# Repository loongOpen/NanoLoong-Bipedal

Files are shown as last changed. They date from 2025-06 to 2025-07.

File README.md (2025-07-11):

# NanoLoong-Bipedal
Building a high-performance bipedal robot that combines Pixar and Disney BDX！
<table>
  <tr>
    <td> </td>
    <td> </td>
    <td> </td>
   </tr> 
</table>

In this project, we combined Pixar's lamp robot and Disney's BDX robot to build a 60cm high-performance Nano bipedal robot.</br>
The entire robot uses a brushless motor, runs a reinforcement learning algorithm and comes with an open source tutorial. The cost of the whole machine is less than 15,000 RMB!</br>
This project will update the latest information in real time in the Feishu link below[https://hcn64ij2s2xr.feishu.cn/wiki/AZJxwlvEpiWnRrkeBbGc21U9n7f]</br>
Detail intro:</br>
https://www.bilibili.com/video/BV1FRZoY1ExW/?spm_id_from=333.337.search-card.all.click

# State of sim2real
The gait of Nano version is highly consistent with the BDX effect ! 

https://private-user-images.githubusercontent.com/16828431/430457828-f0ea37f3-0f17-4512-8b72-3c25d8892571.mp4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

https://private-user-images.githubusercontent.com/16828431/430457885-5fd6a661-4399-4f3d-8686-e99e13dff1be.mp4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

# Updates
> Update 2025/4/5: You can try two policies we trained : Update Nano first release version.

# CAD
https://private-user-images.githubusercontent.com/16828431/430457786-0a5316d1-bd46-40a6-932d-3f43c3e6b83e.mp4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

See [this document](https://hcn64ij2s2xr.feishu.cn/wiki/DPWDwNWaZiGNvpkbRrGcBXCHn7d) for getting from the CAD design of Nano.

# PCB
https://private-user-images.githubusercontent.com/16828431/430457807-14ccab23-9aa0-415d-9c31-68c5db94b0f6.mp4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

See [this document](https://hcn64ij2s2xr.feishu.cn/wiki/DPWDwNWaZiGNvpkbRrGcBXCHn7d) for getting from the PCB design of Nano.

# RL stuff
We are switching to IsaccGym, see this [repo](https://hcn64ij2s2xr.feishu.cn/wiki/LJxZwgL1diHB8ykKU1acFnXknOf)

https://private-user-images.githubusercontent.com/16828431/430457843-6a1d952e-9353-46ef-b826-be9859c01c90.mp4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

https://private-user-images.githubusercontent.com/16828431/430457815-24d15ffc-5014-4805-8926-c6f4ba6477bd.mp4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

## AI xiaozhi with LLM
Robots can install Xiaozhi AI modules to implement large language model functions !

https://private-user-images.githubusercontent.com/16828431/430457854-93e3f5cd-dadc-4843-8eb6-a85532883e98.mp4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

See [this repo](https://github.com/78/xiaozhi-esp32)

# BOM
You can get the BOM list at the link below.
https://hcn64ij2s2xr.feishu.cn/wiki/DPWDwNWaZiGNvpkbRrGcBXCHn7d
# Build Guide
The following is an overview of the robot project.
https://hcn64ij2s2xr.feishu.cn/wiki/AZJxwlvEpiWnRrkeBbGc21U9n7f
## Assembly Guide
The following link is an introduction to the overall project assembly of the robot.
https://hcn64ij2s2xr.feishu.cn/wiki/FqmXwnRYliwYFbkXCO7csSHWnfh
# Software Guide
This repo contains the software to run the policies of TVM on the onboard computer (Odroid C4) https://hcn64ij2s2xr.feishu.cn/wiki/MJ25wew9PijvXlkIoH7cZ9e4nCh
# Training your own policies
If you want to train your own policies, see [this document](https://hcn64ij2s2xr.feishu.cn/wiki/LJxZwgL1diHB8ykKU1acFnXknOf)

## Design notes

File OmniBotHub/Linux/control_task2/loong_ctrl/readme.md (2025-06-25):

程序框架

# 框架核心思想：隔离！

为防止屎山出现，任何添加的功能模块，必须以最小成本、最小作用域的形式进行添加。

# 框架使用（简）

所有常用操作均在tools文件夹内即可完成

* **仿真（x64平台)：**

```
cd tools
./make.sh x      #自动cp生成库到mujoco目录
./run_mujoco.sh  #同mujoco内运行同名脚本，加数字参数可缓速运行
```

* **实机（x64平台编译，arm64平台运行）**

```
cd tools
./make.sh        #自动交叉编译、scp生成库到实机（务必在update_lib.sh中修改scp目标，以免覆盖他人文件夹）
                 #实机内运行./run.sh
```

# 框架结构（简）

框架顶层为状态机fsm

添加功能的最大单位被称为plan，plan在manager内被add进状态机fsm，fsm负责调度所有的plan

为方便操作，manager内采用宏定义区别了仿真与实机plan的切换逻辑

plan内完成各自所需的所有子功能模块，不同plan之间在调度上互相独立

plan之间复用的模块、数据，推荐以单例形式调用

程序初始会调用每个plan的init

程序运行过程中fms会调用plan的进入(hey)、运行(run)、通知退出(bye)、写日志(log)四个接口，plan自身通过运行(run)的返回值负责自身的退出。另外fms会根据plan的优先级强制plan退出

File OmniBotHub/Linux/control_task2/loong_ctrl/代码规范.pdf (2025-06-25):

# 代码规范

机器人代码会涉及大量矩阵运算、行业性控制逻辑等，因此机器人代码风格 应结合机器人控制算法的特征进行规范，而不应一味照搬互联网行业习惯。

## 1. 总则

最小完备性：功能完备，代码最简，每一个字符（包括空白字符）都有价值。 对人：易读。
对机器：高效。

## 2. 文件命名

核心思想：具有辨识度，便于键入与结合 tab 键使用。
① 首字母小写，便于键入。
② 多单词使用下划线分割，便于 tab。
③ 有潜在相似文件夹命名，原始文件夹以下划线结尾，便于拓展。

## 3. 变量命名

核心思想：具有辨识度，结构紧凑，逻辑合理，便于阅读。
① 驼峰命名，不使用下划线，从而避免信息密度过低，整体观感混乱。 ② 除③外一律首字母小写，便于键入。
③ 仅两种情况允许首字母大写：
(A) 矩阵，匹配数学含义一目了然。
(B) 具有全局意义的量：namespace、#define、const 等。其中#define 使用 大驼峰，严禁全大写，造成阅读不便

④ class、struct 本体定义以-Class、-Struct 结尾。其中：
struct 用于数据结构，可包含 init、reset 等基本方法，不包含复杂逻辑。 class 用于具备逻辑运算功能的封装。
④ 固定一些常用缩写词缀：tgt-、act-、est-等前缀，-P、-V、-F 等后缀。

## 4. 代码结构

核心思想：结构紧凑节约屏幕空间，逻辑合理，便于阅读。
① if、for 等即便仅有单行函数体也必须加花空号，便于阅读与二次拓展，

避免错位。
② 函数的左花括号紧跟主体，而不是另起一行，以充分利用屏幕纵向空间 的有效行数。
③ 任何表达式中，不用无意义空格。空格仅用于计算逻辑分割或对齐，例 如：

## 5. 逻辑结构

核心思想：结构逻辑合理，便于人类阅读以及机器效率。
① 模块功能封装（面向对象）。
② 调用逻辑紧凑（面向过程）。
④ 不常用的库不要 include 到*.h 文件污染全局。可采用 imp 封装在.cpp 内。 ⑤ 减少继承、飞针（指针传递）使用，包括传统指针和现代指针在内的 cast、 move 语义等，避免造成阅读识别障碍与阅读逻辑混淆。
⑥ 避免对象或函数过多层级、多文件分散嵌套，造成阅读障碍。

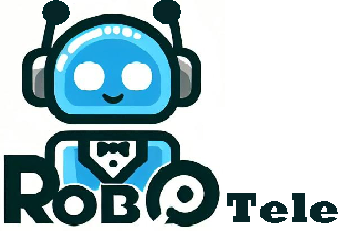
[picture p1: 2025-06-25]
OmniBotTele/ESP32/assets/无标题(1).png

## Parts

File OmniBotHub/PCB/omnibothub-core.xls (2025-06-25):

Comment | Description | Designator | Footprint | Quantity
Header 2 | 公口 XT侧端子 | BAT | AMASS-XT30PW-M | 1
Header 6 | 2.54排针 | BAT_O | HDR1X6 | 1
BEEP |  | BEEP? | DET402 | 1
Header 2 | Header, 2-Pin | BOOT1 | 663*4*2.0/2.5MM | 1
0.1UF | 贴片电容 | C1, C9, C11, C12, C14, C15, C16, C17, C18, C21 | C 0402 | 10
1UF | 贴片电容 | C2 | C 0402 | 1
2.2UF | 贴片电容 | C3, C4 | C0603 | 2
10NF | 贴片电容 | C5 | C 0402 | 1
20PF | 贴片电容 | C6, C7 | C 0402 | 2
0.1UF | 贴片电容 | C8, C19, C20 | C0603 | 3
10uF | 贴片电容 | C10, C13 | C0603 | 2
100uF | 贴片电容 | C27 | C0805 | 1
Header 4 | 立端子母口 | CAN1, CAN2, CAN3, CAN4 | AMASS-XT30(2+2)PW-M_V2 - LI | 4
BAT54WS | 单肖特基二极管 | D1 | SOD-323 | 1
PESD1CAN |  | D2, D3 | SOT-23 | 2
LED1 | LED蓝色 | DS1, DS2 | SMDLED | 2
ICM20602 |  | ICM1 | ICM20602 | 1
Header 2 | 立端子 | LED_C, LED_S | GH1.25-2P | 2
Header 3 | XH立端子 缺口朝向丝印 | LED_L, LED_R | HDR1X3 | 2
Header 5 | 2.54母座 | P2 | HDR1X5 | 1
Header 4 | 2.54母座 | P3 | HDR1X4 | 1
Header 5X2 | 2.54母座双排 | PIO | HDR2X5 | 1
S8050 | 8050/BCW846/BCW847 | Q1, Q2 | SOT-23R | 2
10K | 贴片电阻 | R1, R2, R3, R4, R7 | R0603 | 5
560R | 贴片电阻 | R5, R20 | R0603 | 2
1K | 贴片电阻 | R6 | R0603 | 1
100R | 贴片电阻 | R8, R9 | R0603 | 2
120R | 贴片电阻 | R12, R17 | R0603 | 2
100K | 贴片电阻 | R18 | R0805 | 1
10K | 贴片电阻 | R19, R21 | R0805 | 2
360R | 贴片电阻 | R22, R24 | R 0402 | 2
120R | 贴片电阻 | R23 | R 0402 | 1
Header 4 | 立端子 | R485, SERVO_UART, WHEEL_UART | JST_GH_V4 | 3
Header 2 | 侧按键 | RST | KEY_SAD | 1
Header 3 | 立端子 | SBUS | JST_GH_V3 | 1
Header 4 | 卧贴端子 | SWD1, USB_L1 | SH1.0-4P - UP | 2
STM32F405RGT6 |  | U1 | LQFP64_M | 1
W25X16 | W25X16;SST25VF016;MX25L1605 | U2 | W25Q32FVZPIG | 1
TJA1050 |  | U3, U4 | SOP-8 | 2
SP3485 |  | U5 | SOP-8 | 1
RT9193-3.3/LP2985/SPX3819 | 降压IC | V1 | SOT23-5 | 1
8MHZ | Crystal Oscillator | X1 | PXCL | 1

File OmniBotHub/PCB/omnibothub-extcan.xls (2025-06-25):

Comment | Description | Designator | Footprint | Quantity
Header 2 | 2.54白色端子 立 | BAT | HDR1X2 | 1
Header 2 | 贴片按键 | BOOT1 | 663*4*2.0/2.5MM | 1
0.1UF | 贴片电容 | C1, C9, C11, C12, C14, C15, C16, C17, C18, C21 | C 0402 | 10
1UF | 贴片电容 | C2 | C 0402 | 1
2.2UF | 贴片电容 | C3, C4 | C0603 | 2
10NF | 贴片电容 | C5 | C 0402 | 1
20PF | 贴片电容 | C6, C7 | C 0402 | 2
0.1UF | 贴片电容 | C8 | C0603 | 1
10uF | 贴片电容 | C10, C13 | C0603 | 2
Header 4 | 立贴端子 | CAN1, CAN3, R485 | PH2.0-4SMT | 3
BAT54WS | 单肖特基二极管 | D1 | SOD-323 | 1
PESD1CAN |  | D2, D3 | SOT-23 | 2
LED1 | LED 蓝色 | DS1, DS2 | SMDLED | 2
Header 5X2 | 2.54排针,长度8mm | PIO | HDR2X5 | 1
10K | 贴片电阻 | R1, R2, R4 | R0603 | 3
100R | 贴片电阻 | R8, R9 | R0603 | 2
120R | 贴片电阻 | R12, R17 | R0603 | 2
360R | 贴片电阻 | R22, R24 | R 0402 | 2
120R | 贴片电阻 | R23 | R 0402 | 1
Header 4 | 卧贴端子 | SWD1, USB_L1 | SH1.0-4P - UP | 2
STM32F405RGT6 |  | U1 | LQFP64_M | 1
W25X16 | W25X16;SST25VF016;MX25L1605 | U2 | W25Q32FVZPIG | 1
TJA1050 |  | U3, U4 | SOP-8 | 2
SP3485 |  | U5 | SOP-8 | 1
RT9193-3.3/LP2985/SPX3819 | 降压IC | V1 | SOT23-5 | 1
8MHZ | Crystal Oscillator | X1 | PXCL | 1

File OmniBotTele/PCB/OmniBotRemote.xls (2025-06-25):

Comment | Description | Designator | Footprint | Quantity
TP4059 | TP4059 | B1 | SOT23-6S | 1
1UF | 贴片电容 | C1, C3 | C 0402 | 2
0.1UF | 贴片电容 | C2, C4, C5, C11, C17, C20 | C 0402 | 6
20PF | 贴片电容 | C6, C7 | C 0402 | 2
0.1UF | 贴片电容 | C13 | C0603 | 1
10UF | 贴片电容 | C14, C16, C19 | C0603 | 3
22uF | 贴片电容 | C15 | C 0402 | 1
IN4733 5.1V | Zener Diode | D1 | 1n4148-SOD123 | 1
BAT54WS | 单肖特基二极管 | D2 | SOD-323 | 1
LED1 | LED 蓝色 | DS1, DS2, DS3, DS4 | SMDLED | 4
方向摇杆 | 摇杆 | J1, J2 | 摇杆2 | 2
KEY_M | 立按键，按键长度8mm | KEY1, KEY2, KEY3, KEY4 | KEY_M | 4
DS0 | LED红色 | LED1 | LED_0603 | 1
Header 3 | 三挡开关 立直插 | P3, | HDR1X3 | 1 | https://item.taobao.com/item.htm?id=44894134662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
1K | 贴片电阻 | R1, R8 | R 0402 | 2
1K | 贴片电阻 | R9, R10 | R0603 | 2
4.7K | 贴片电阻 | R11, R12 | R 0402 | 2
100R | 贴片电阻 | R13, R14, R15, R16 | R0603 | 4
Header 4 | 卧贴端子 | SWD1 | SH1.0-4P - UP | 1
STM32F103C8 |  | U1 | LQFP48S | 1
USB-B(Mini) |  | USB | USB/SM0.8-6H5_M | 1
RT9193-3.3/LP2985/SPX3819 | 降压IC | V1 | SOT23-5 | 1
8MHZ | Crystal Oscillator | X1 | PXCL | 1

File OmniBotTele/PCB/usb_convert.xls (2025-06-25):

Comment | Description | Designator | Footprint | Quantity
Header 4 | 2.54排针 | P1 | HDR1X4 | 1
USB-B(Mini) | USB Micro端子 | USB1, USB1SWD | USB/SM0.8-6H5_M | 2
Header 4 | SH1.0 卧贴 | USB_L1, USB_R1 | SH1.0-4P | 2

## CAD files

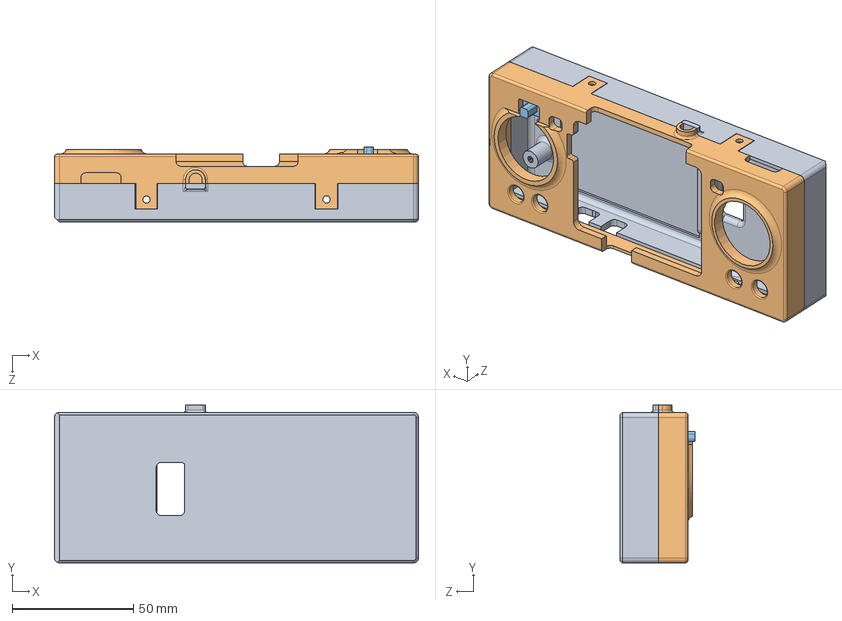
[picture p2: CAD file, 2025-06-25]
OmniBotTele/外壳/遥控器.SLDASM
150.0 x 65.0 x 31.0 mm
底座
上盖
开关

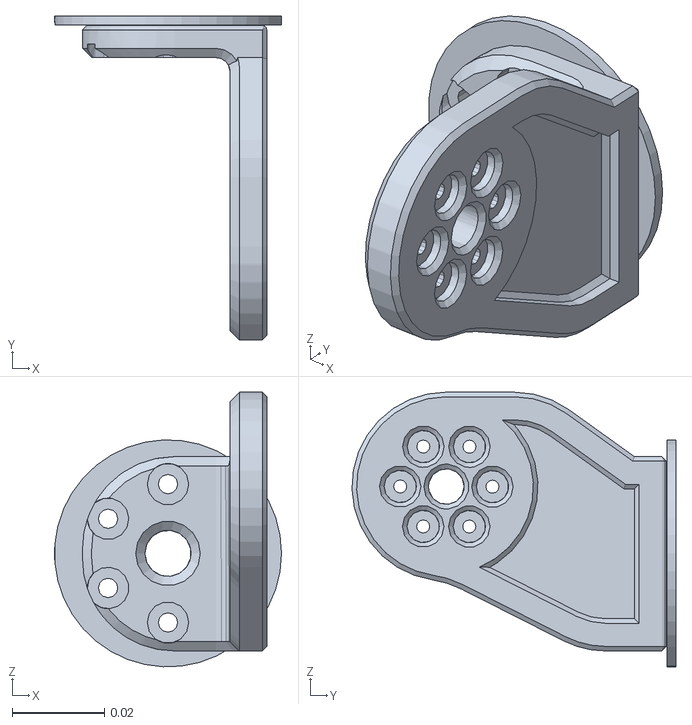
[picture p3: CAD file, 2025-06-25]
OmniBotCtrl/OmniBotCtrl/resources/taitan/meshes/L1_Link.STL
0.0492 x 0.0703 x 0.0595

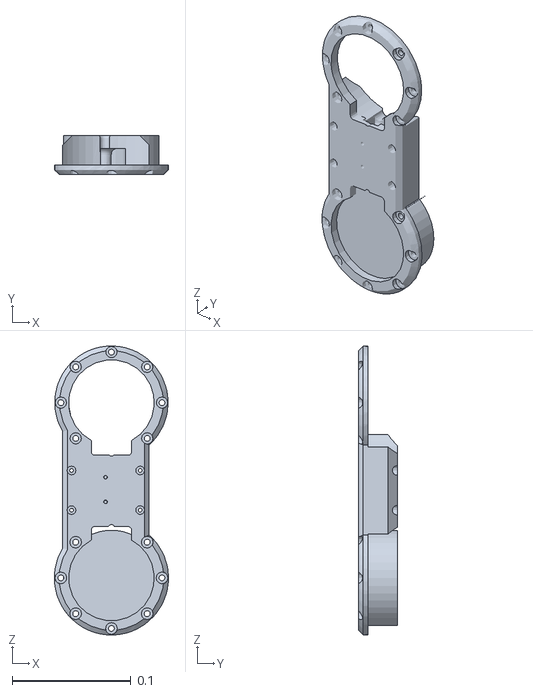
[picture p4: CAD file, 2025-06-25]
OmniBotCtrl/OmniBotCtrl/resources/tinker/meshes/link_r_pitch.STL
0.096 x 0.033 x 0.243

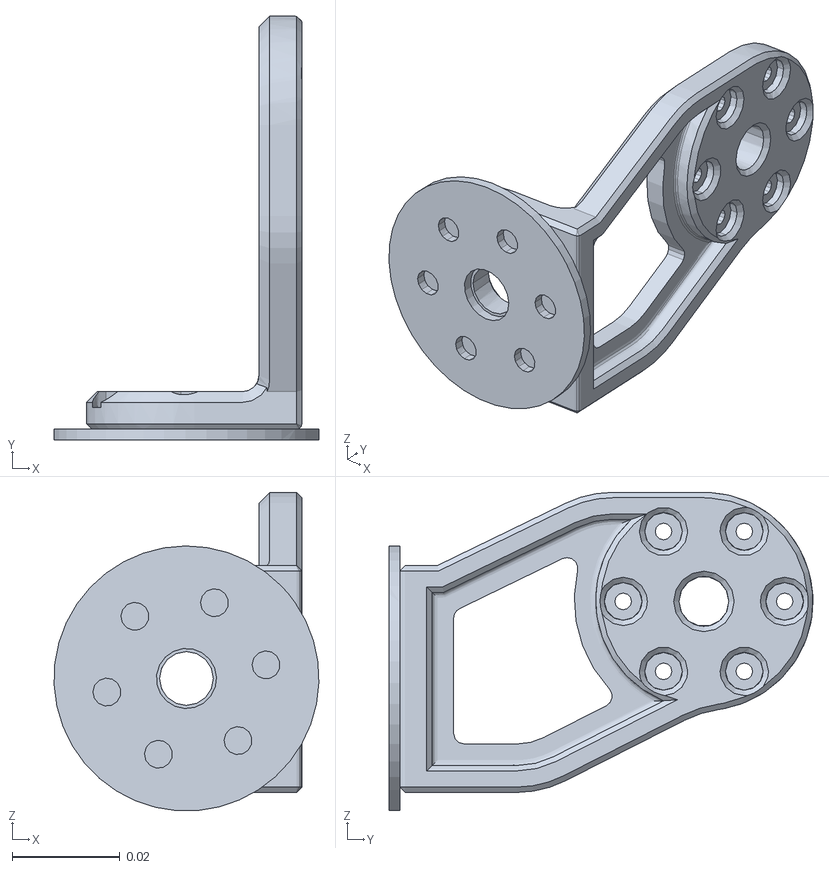
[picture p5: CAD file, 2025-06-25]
OmniBotCtrl/OmniBotCtrl/resources/TinkerV2_URDF/meshes/R1_Link.STL
0.0492 x 0.0788 x 0.0591

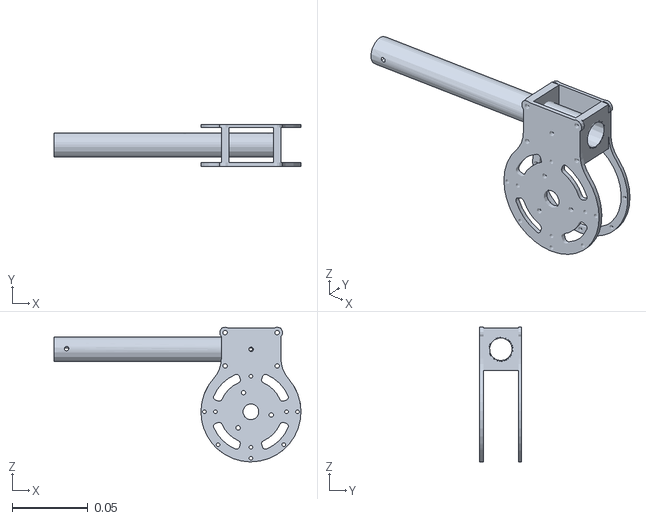
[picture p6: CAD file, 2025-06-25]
OmniBotCtrl/OmniBotCtrl/resources/tinymal/meshes/RR_calf.STL
0.163 x 0.0275 x 0.089

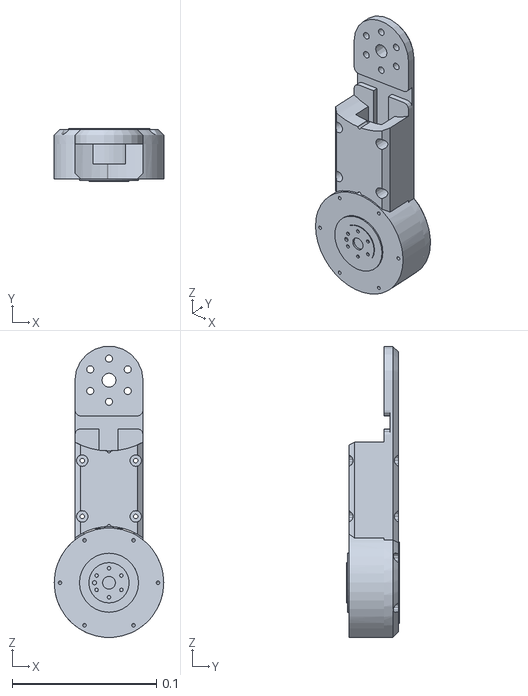
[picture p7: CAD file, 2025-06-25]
OmniBotSeries/URDF/TinkerV2_URDF/meshes/R3_Link.STL
0.076 x 0.0365 x 0.202

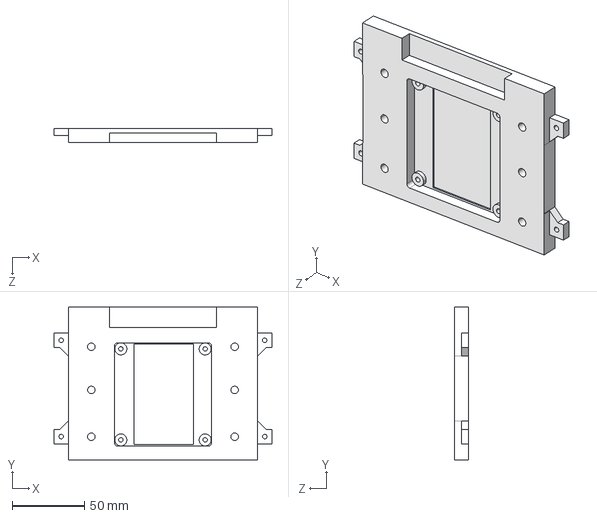
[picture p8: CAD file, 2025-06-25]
OmniBotSeries/切割/机体2.STEP
151.0 x 105.7 x 10.0 mm

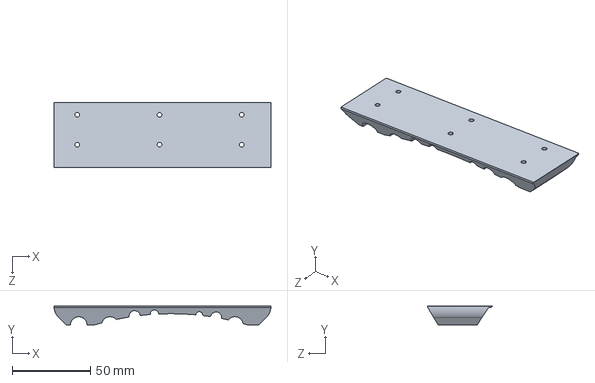
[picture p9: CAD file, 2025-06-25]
OmniBotSeries/打印/back/足底 DC 硬度50.STEP
138.9 x 12.1 x 41.8 mm

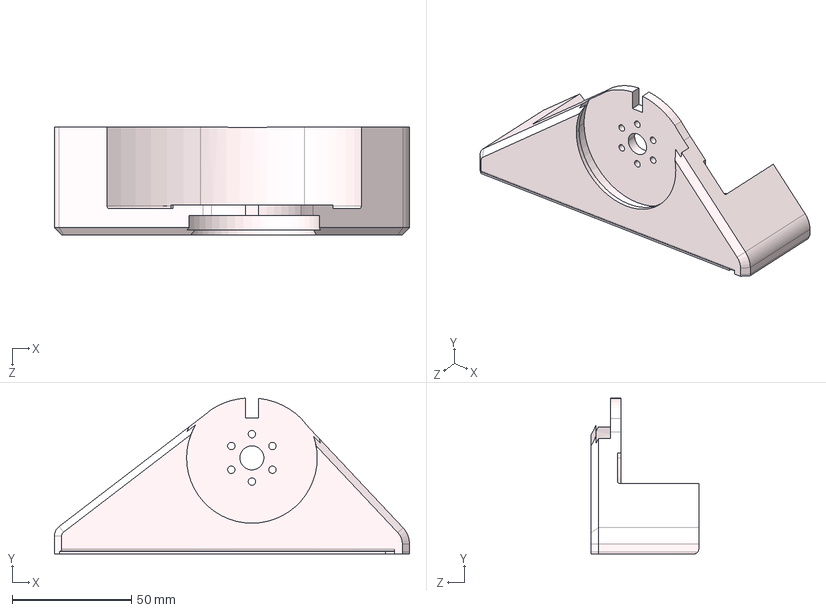
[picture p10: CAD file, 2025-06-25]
OmniBotSeries/打印/足端4 包胶 -长.STEP
148.5 x 65.2 x 45.0 mm

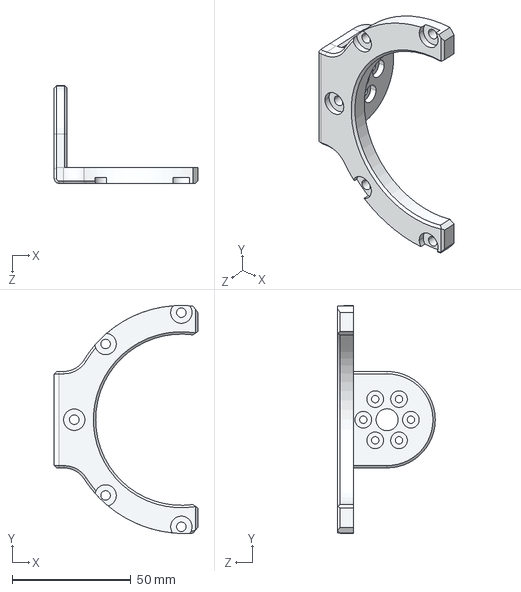
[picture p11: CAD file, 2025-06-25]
OmniBotSeries/机加工/hip 2个.STEP
60.3 x 95.8 x 41.0 mm

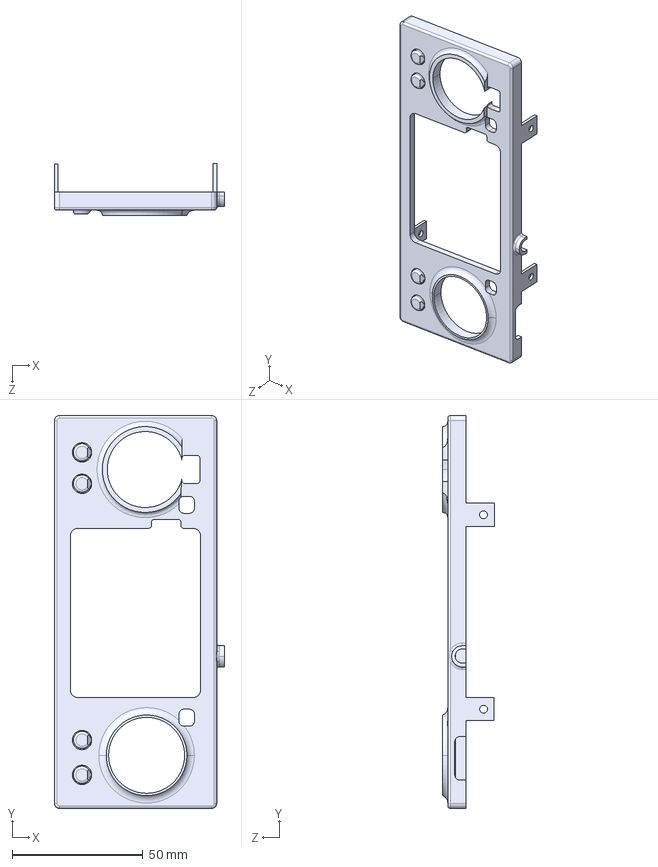
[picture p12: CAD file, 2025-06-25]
OmniBotTele/外壳/上盖 - 矮.STEP
65.0 x 150.0 x 19.8 mm

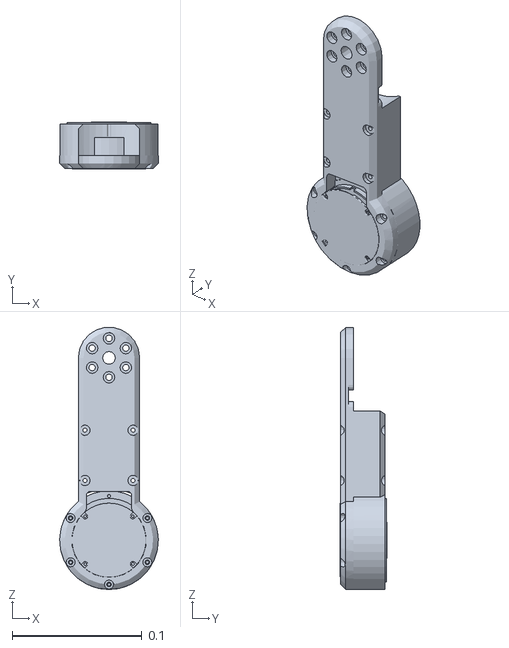
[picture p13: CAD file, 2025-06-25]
OmniBotCtrl/OmniBotCtrl/resources/taitan/meshes/L3_Link.STL
0.076 x 0.0365 x 0.202

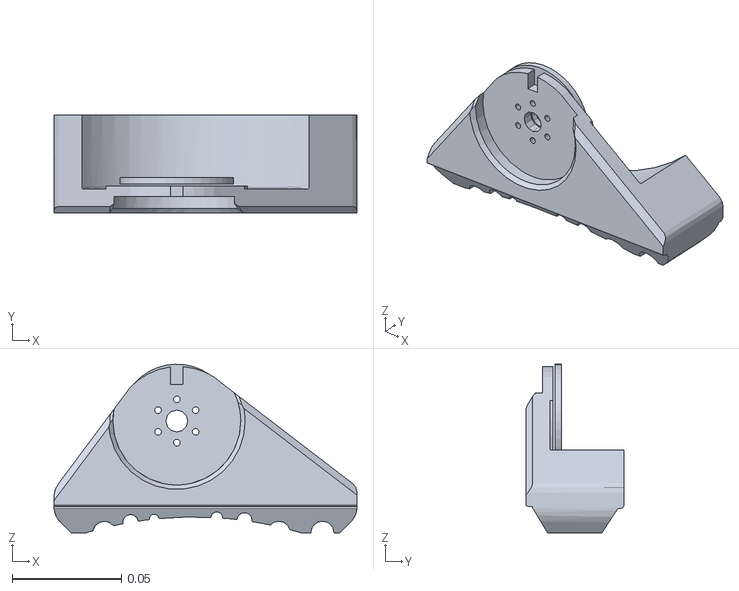
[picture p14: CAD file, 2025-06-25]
OmniBotCtrl/OmniBotCtrl/resources/tinker/meshes/link_r_ankle.STL
0.139 x 0.045 x 0.0773

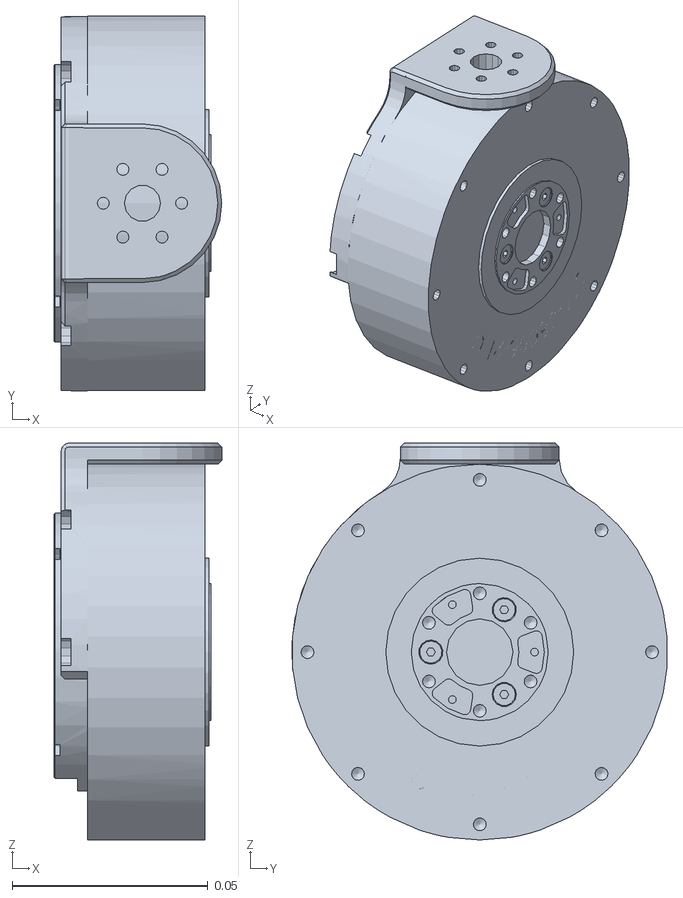
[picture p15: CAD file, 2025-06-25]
OmniBotCtrl/OmniBotCtrl/resources/TinkerV2_URDF/meshes/R0_Link.STL
0.0428 x 0.0958 x 0.101

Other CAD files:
OmniBotCtrl/OmniBotCtrl/resources/tinymal/meshes/FR_thigh.STL
OmniBotSeries/URDF/TinkerV2_URDF/meshes/L0_Link.STL
OmniBotSeries/切割/大腿2个.STEP
OmniBotSeries/打印/back/足端3 DC.STEP
OmniBotCtrl/OmniBotCtrl/resources/TinkerV2_URDF/meshes/L0_Link.STL
OmniBotCtrl/OmniBotCtrl/resources/TinkerV2_URDF/meshes/L1_Link.STL
OmniBotCtrl/OmniBotCtrl/resources/TinkerV2_URDF/meshes/L2_Link.STL
OmniBotCtrl/OmniBotCtrl/resources/TinkerV2_URDF/meshes/L3_Link.STL
OmniBotCtrl/OmniBotCtrl/resources/TinkerV2_URDF/meshes/L4_Link_ankle.STL
OmniBotCtrl/OmniBotCtrl/resources/TinkerV2_URDF/meshes/R2_Link.STL
OmniBotCtrl/OmniBotCtrl/resources/TinkerV2_URDF/meshes/R4_Link_ankle.STL
OmniBotCtrl/OmniBotCtrl/resources/TinkerV2_URDF/meshes/base_link.STL
OmniBotCtrl/OmniBotCtrl/resources/taitan/meshes/L0_Link.STL
OmniBotCtrl/OmniBotCtrl/resources/taitan/meshes/L2_Link.STL
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

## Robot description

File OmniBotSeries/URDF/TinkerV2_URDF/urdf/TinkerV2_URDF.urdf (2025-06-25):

<?xml version="1.0" encoding="utf-8"?>
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
<robot name="TinkerV2_URDF">
  <link name="base_link">
    <inertial>
      <origin xyz="0.0191973307162497 -0.000897919994656132 0.0759941643862994" rpy="0 0 0" />
      <mass value="4.72255223919314" />
      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
    </inertial>
    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
  </link>
  <link name="L0_Link">
    <inertial>
      <origin xyz="0.000619765634653893 4.28150829746982E-05 -0.0528764064151365" rpy="0 0 0" />
      <mass value="0.587331353457417" />
      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
    </inertial>
    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
  </link>
  <joint name="J_L0" type="revolute">
    <origin xyz="-0.002787 0.053542 0.054381" rpy="0 0 0" />
    <parent link="base_link" />
    <child link="L0_Link" />
    <axis xyz="0 0 1" />
    <limit lower="-1.57" upper="1.57" effort="12" velocity="20" />
  </joint>
  <link name="L1_Link">
    <inertial>
      <origin xyz="-0.00347150340744003 0.0341575635250294 -0.00920422354080709" rpy="0 0 0" />
      <mass value="0.0295521887544817" />
      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
    </inertial>
    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
  </link>
  <joint name="J_L1" type="revolute">
    <origin xyz="0.016958 0 -0.053917" rpy="0 0 0" />
    <parent link="L0_Link" />
    <child link="L1_Link" />
    <axis xyz="-1 0 0" />
    <limit lower="-1.57" upper="1.57" effort="20" velocity="20" />
  </joint>
  <link name="L2_Link">
    <inertial>
      <origin xyz="-0.000792134004393902 0.0178195463367404 -0.0737982008261337" rpy="0 0 0" />
      <mass value="1.34863094594399" />
      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
    </inertial>
    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
  </link>
  <joint name="J_L2" type="revolute">
    <origin xyz="-0.012958 0.059001 -0.014313" rpy="0 0 0" />
    <parent link="L1_Link" />
    <child link="L2_Link" />
    <axis xyz="0 1 0" />
    <limit lower="-1.57" upper="1.57" effort="20" velocity="20" />
  </joint>
  <link name="L3_Link">
    <inertial>
      <origin xyz="-4.78959695469905E-06 0.00800400502048923 -0.121850966704469" rpy="0 0 0" />
      <mass value="0.629727076499127" />
      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
    </inertial>
    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
  </link>
  <joint name="J_L3" type="revolute">
    <origin xyz="0 0 -0.14738" rpy="0 0 0" />
    <parent link="L2_Link" />
    <child link="L3_Link" />
    <axis xyz="0 1 0" />
    <limit lower="-1.57" upper="1.57" effort="20" velocity="20" />
  </joint>
  <link name="L4_Link_ankle">
    <inertial>
      <origin xyz="0.0117863373334438 -0.00675302646643325 -0.0296425502455308" rpy="0 0 0" />
      <mass value="0.171742682777178" />
      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
    </inertial>
    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
  </link>
  <joint name="J_L4_ankle" type="revolute">
    <origin xyz="0 0.025 -0.14049" rpy="0 0 0" />
    <parent link="L3_Link" />
    <child link="L4_Link_ankle" />
    <axis xyz="0 -1 0" />
    <limit lower="-1.57" upper="1.57" effort="12" velocity="20" />
  </joint>
  <link name="R0_Link">
    <inertial>
      <origin xyz="0.000619765633283198 -6.07774382760072E-05 -0.0528236158498482" rpy="0 0 0" />
      <mass value="0.587331353381893" />
      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
    </inertial>
    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
  </link>
  <joint name="J_R0" type="revolute">
    <origin xyz="-0.002787 -0.053184 0.054381" rpy="0 0 0" />
    <parent link="base_link" />
    <child link="R0_Link" />
    <axis xyz="0 0 1" />
    <limit lower="-1.57" upper="1.57" effort="12" velocity="20" />
  </joint>
  <link name="R1_Link">
    <inertial>
      <origin xyz="-0.00347132375249927 -0.034156693924089 -0.0092040577765706" rpy="0 0 0" />
      <mass value="0.029551251476222" />
      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
    </inertial>
    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
  </link>
  <joint name="J_R1" type="revolute">
    <origin xyz="0.016958 0 -0.053917" rpy="0 0 0" />
    <parent link="R0_Link" />
    <child link="R1_Link" />
    <axis xyz="-1 0 0" />
    <limit lower="-1.57" upper="1.57" effort="20" velocity="20" />
  </joint>
  <link name="R2_Link">
    <inertial>
      <origin xyz="-0.000791325692475933 -0.0178404338194351 -0.0737102397834983" rpy="0 0 0" />
      <mass value="1.35023891621348" />
      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
    </inertial>
    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
  </link>
  <joint name="J_R2" type="revolute">
    <origin xyz="-0.012958 -0.059 -0.014313" rpy="0 0 0" />
    <parent link="R1_Link" />
    <child link="R2_Link" />
    <axis xyz="0 -1 0" />
    <limit lower="-1.57" upper="1.57" effort="20" velocity="-2" />
  </joint>
  <link name="R3_Link">
    <inertial>
      <origin xyz="2.2396603683833E-05 -0.00733283067364296 -0.117588903345598" rpy="0 0 0" />
      <mass value="0.511661896307101" />
      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
    </inertial>
    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
  </link>
  <joint name="J_R3" type="revolute">
    <origin xyz="0 0 -0.14738" rpy="0 0 0" />
    <parent link="R2_Link" />
    <child link="R3_Link" />
    <axis xyz="0 -1 0" />
    <limit lower="-1.57" upper="1.57" effort="20" velocity="20" />
  </joint>
  <link name="R4_Link_ankle">
    <inertial>
      <origin xyz="0.011786 0.0067411 -0.029643" rpy="0 0 0" />
      <mass value="0.17174" />
      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
    </inertial>
    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
  </link>
  <joint name="J_R4_ankle" type="revolute">
    <origin xyz="0 -0.025 -0.14049" rpy="0 0 0" />
    <parent link="R3_Link" />
    <child link="R4_Link_ankle" />
    <axis xyz="0 1 0" />
    <limit lower="-1.57" upper="1.57" effort="12" velocity="20" />
  </joint>
</robot>

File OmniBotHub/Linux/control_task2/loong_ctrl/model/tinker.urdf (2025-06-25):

<?xml version="1.0" encoding="utf-8"?>
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
<robot name="tinker_urdf">
  <mujoco>
    <compiler meshdir="meshes/" balanceinertia="true" discardvisual="false" />
  </mujoco>
  <link name="base_link">
    <inertial>
      <origin xyz="-0.030485 0.000283 0.020881" rpy="0 0 0" />
      <mass value="2.3933" />
      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 
    </inertial>
    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
  </link>
  <link name="link_l_yaw">
    <inertial>
      <origin xyz="0.0031721 3.773E-05 -0.050777" rpy="0 0 0" />
      <mass value="0.4033" /> 
      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
    </inertial>
    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
  </link>
  <joint name="joint_l_yaw" type="revolute">
    <origin xyz="0.0025357 0.053301 0.056145" rpy="0 0 0" />
    <parent link="base_link" />
    <child link="link_l_yaw" />
    <axis xyz="0 0 1" />
    <limit lower="-0.66" upper="0.66" effort="12" velocity="20" />
  </joint>
  <link name="link_l_roll">
    <inertial>
      <origin xyz="0.0090994 0.06545 -0.013394" rpy="0 0 0" />
      <mass value="0.46748" />
      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
    </inertial>
    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
  </link>
  <joint name="joint_l_roll" type="revolute">
    <origin xyz="-0.010958 0 -0.054965" rpy="0 0 0" />
    <parent link="link_l_yaw" />
    <child link="link_l_roll" />
    <axis xyz="1 0 0" />
    <limit lower="-0.57" upper="0.57" effort="20" velocity="20" />
  </joint>
  <link name="link_l_pitch">
    <inertial>
      <origin xyz="-0.0013138 0.0056716 -0.12051" rpy="0 0 0" />
      <mass value="0.56676" />
      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
    </inertial>
    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
  </link>
  <joint name="joint_l_pitch" type="revolute">
    <origin xyz="0.010958 0.071699 -0.014313" rpy="0 0 0" />
    <parent link="link_l_roll" />
    <child link="link_l_pitch" />
    <axis xyz="0 1 0" />
    <limit lower="-1.57" upper="0.57" effort="20" velocity="20" />
  </joint>
  <link name="link_l_knee">
    <inertial>
      <origin xyz="-2.3595E-06 -0.0058981 -0.11387" rpy="0 0 0" />
      <mass value="0.35345" />
      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
    </inertial>
    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
  </link>
  <joint name="joint_l_knee" type="revolute">
    <origin xyz="0 0 -0.14738" rpy="0 0 0" />
    <parent link="link_l_pitch" />
    <child link="link_l_knee" />
    <axis xyz="0 1 0" />
    <limit lower="0" upper="2.57" effort="20" velocity="20" />
  </joint>
  <link name="link_l_ankle">
    <inertial>
      <origin xyz="0.020853 0.0048146 -0.030186" rpy="0 0 0" />
      <mass value="0.17624" />
      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
    </inertial>
    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
  </link>
  <joint name="joint_l_ankle" type="revolute">
    <origin xyz="0 0 -0.14049" rpy="0 0 0" />
    <parent link="link_l_knee" />
    <child link="link_l_ankle" />
    <axis xyz="0 1 0" />
    <limit lower="-1.57" upper="0.57" effort="12" velocity="20" />
  </joint>
  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


  <link name="link_r_yaw">
    <inertial>
      <origin xyz="0.0031721 3.773E-05 -0.050777" rpy="0 0 0" />
      <mass value="0.4033" />
      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
    </inertial>
    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
  </link>
  <joint name="joint_r_yaw" type="revolute">
    <origin xyz="0.0025357 -0.053425 0.056145" rpy="0 0 0" />
    <parent link="base_link" />
    <child link="link_r_yaw" />
    <axis xyz="0 0 1" />
    <limit lower="-0.66" upper="0.66" effort="12" velocity="20" />
  </joint>
  <link name="link_r_roll">
    <inertial>
      <origin xyz="0.0090994 -0.06469 -0.013394" rpy="0 0 0" />
      <mass value="0.46748" />
      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
    </inertial>
    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
  </link>
  <joint name="joint_r_roll" type="revolute">
    <origin xyz="-0.010958 0 -0.054965" rpy="0 0 0" />
    <parent link="link_r_yaw" />
    <child link="link_r_roll" />
    <axis xyz="1 0 0" />
    <limit lower="-0.57" upper="0.57" effort="20" velocity="20" />
  </joint>
  <link name="link_r_pitch">
    <inertial>
      <origin xyz="-0.0013138 -0.0047951 -0.11962" rpy="0 0 0" />
      <mass value="0.56676" />
      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
    </inertial>
    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
  </link>
  <joint name="joint_r_pitch" type="revolute">
    <origin xyz="0.010958 -0.071575 -0.014313" rpy="0 0 0" />
    <parent link="link_r_roll" />
    <child link="link_r_pitch" />
    <axis xyz="0 1 0" />
    <limit lower="-1.57" upper="0.57" effort="20" velocity="20" />
  </joint>
  <link name="link_r_knee">
    <inertial>
      <origin xyz="7.3527E-06 0.0067747 -0.11375" rpy="0 0 0" />
      <mass value="0.35345" />
      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
    </inertial>
    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
  </link>
  <joint name="joint_r_knee" type="revolute">
    <origin xyz="0 0 -0.14738" rpy="0 0 0" />
    <parent link="link_r_pitch" />
    <child link="link_r_knee" />
    <axis xyz="0 1 0" />
    <limit lower="0" upper="2.57" effort="20" velocity="20" />
  </joint>
  <link name="link_r_ankle">
    <inertial>
      <origin xyz="0.014562 -0.0039946 -0.031306" rpy="0 0 0" />
      <mass value="0.175" />
      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
    </inertial>
    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
  </link>
  <joint name="joint_r_ankle" type="revolute">
    <origin xyz="0 0 -0.14049" rpy="0 0 0" />
    <parent link="link_r_knee" />
    <child link="link_r_ankle" />
    <axis xyz="0 1 0" />
    <limit lower="-1.57" upper="0.57" effort="12" velocity="20" />
  </joint>

  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
</robot>

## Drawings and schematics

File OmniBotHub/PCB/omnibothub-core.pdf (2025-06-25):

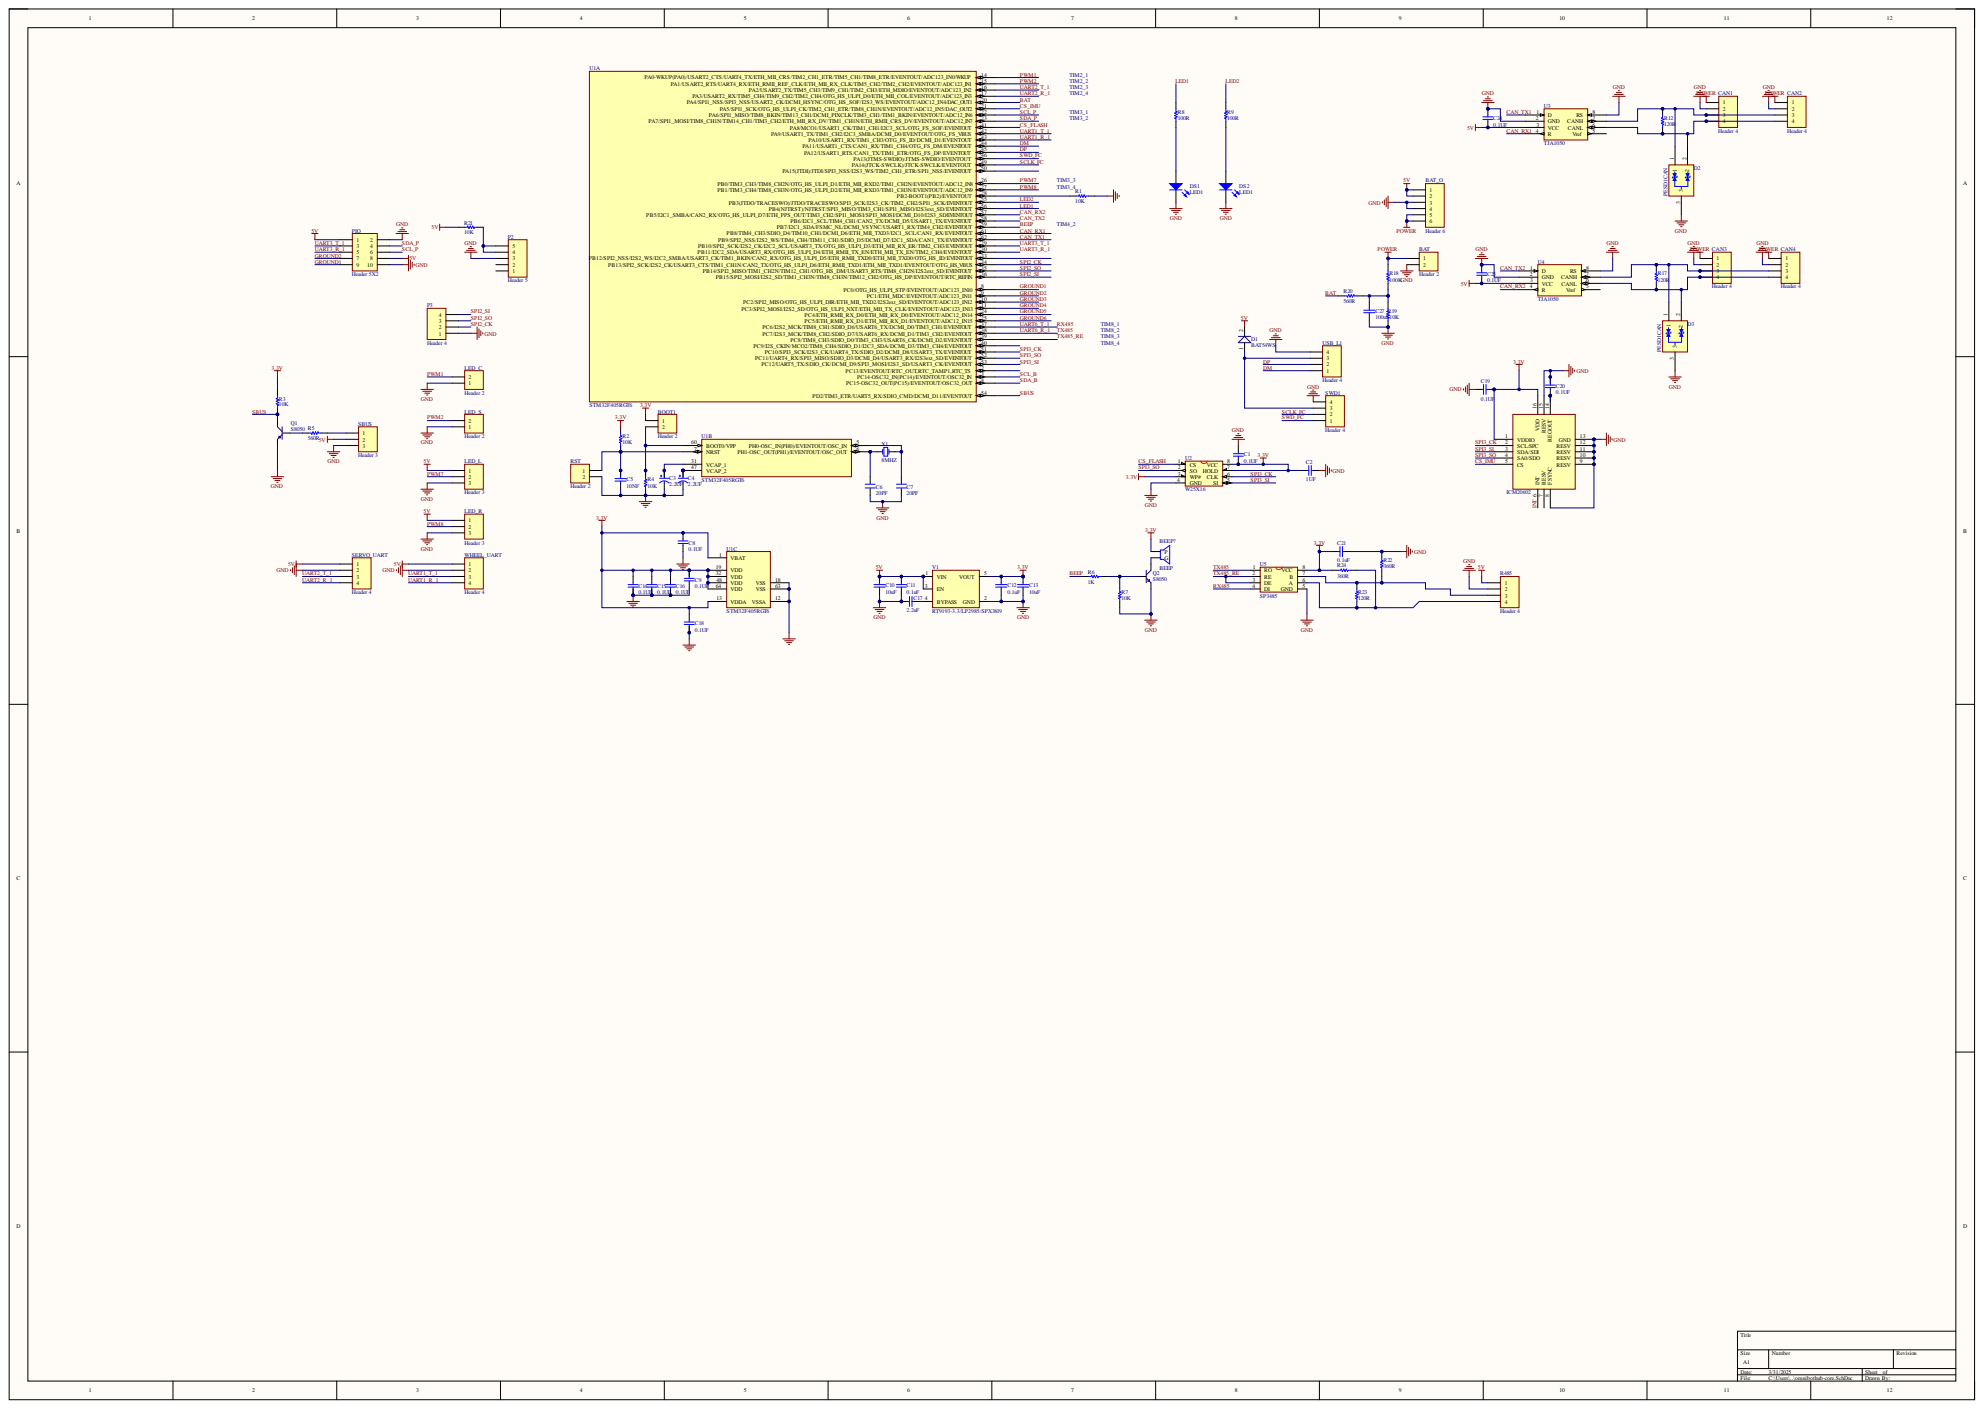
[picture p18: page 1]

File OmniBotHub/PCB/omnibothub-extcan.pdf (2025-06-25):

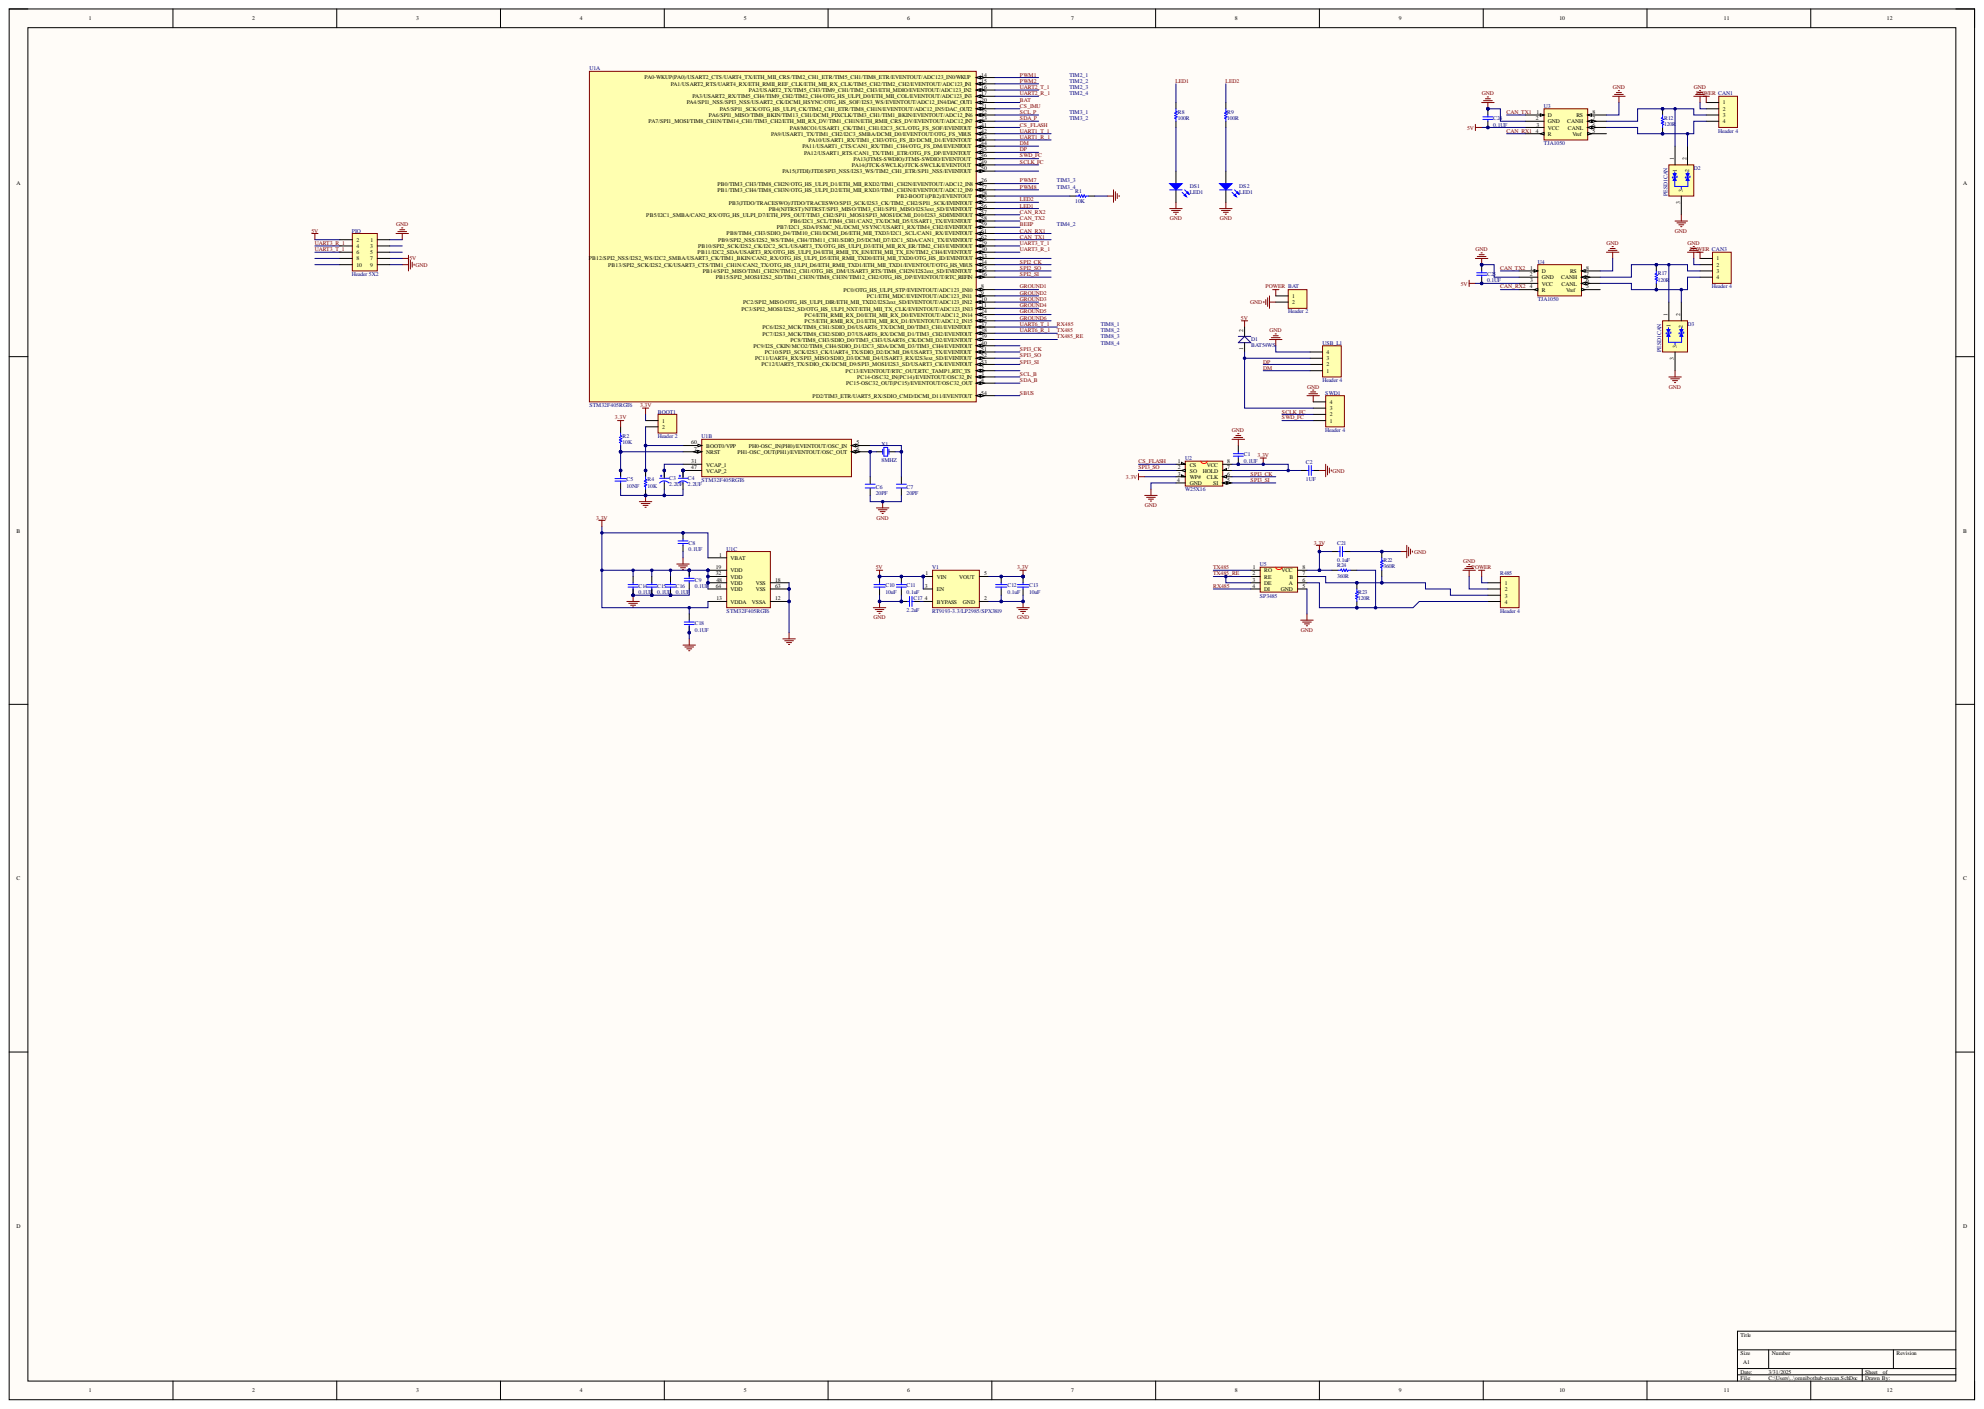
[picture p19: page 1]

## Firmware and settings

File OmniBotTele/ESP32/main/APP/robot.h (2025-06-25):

#ifndef __ROBOT_H
#define __ROBOT_H
#include <stdio.h>
#include <string.h>
#include "wifi_config.h"
#include "ui.h"
#include "ui_helpers.h"
#if 1
    extern lv_obj_t *label;
    extern const char *full_text;
    extern char display_text[64];  // 用于存放增量显示的文本
    extern int current_index;  // 当前显示的字符索引
    extern lv_obj_t *label;
    extern lv_obj_t *tab1;
    extern void increment_text(void);
#endif

#define LV_COLOR_RED        lv_color_hex(0xFF0000)  // 红色
#define LV_COLOR_GREEN      lv_color_hex(0x00FF00)  // 绿色
#define LV_COLOR_BLUE       lv_color_hex(0x0000FF)  // 蓝色
#define LV_COLOR_BLACK      lv_color_hex(0x000000)  // 黑色
#define LV_COLOR_WHITE      lv_color_hex(0xFFFFFF)  // 白色
#define LV_COLOR_GRAY       lv_color_hex(0x808080)  // 灰色
#define LV_COLOR_YELLOW     lv_color_hex(0xFFFF00)  // 黄色
#define LV_COLOR_PURPLE     lv_color_hex(0x800080)  // 紫色
#define LV_COLOR_CYAN       lv_color_hex(0x00FFFF)  // 青色
#define LV_COLOR_MAGENTA    lv_color_hex(0xFF00FF)  // 品红
#define LV_COLOR_ORANGE     lv_color_hex(0xFFA500)  // 橙色
#define LV_COLOR_LIME       lv_color_hex(0x00FF00)  // 亮绿色

typedef struct
{
    char connect;
    int loss_cnt;
    char gait_mode;
    char auto_mode;
    char head_mode;
    char step_mode;
    char heart_cnt;
    float att[3];
    float vel[3];
    float acc[3];
    float gyro[3];
    float mag[3];
    float baro;
    float pos[3];
    float q_leg[14];   
    float q_arm[14];       
    esp_ip4_addr_t ip;                                                                   
} _robot_fb;

extern _robot_fb robot_fb;

typedef struct
{
    char gait_mode;
    char auto_mode;
    char head_mode;
    char step_mode;
    char cal_mode;
    char cal_sel;
    float att[3];
    float vel[3];
    float pos[3];    
    int key_rc[4];
    int power_cnt;                                                                     
} _robot_cmd;

extern _robot_cmd robot_cmd;

typedef struct
{
    char wifi_connected;
    char udp_connected;
    char keyboard_input_sel;
    char cal_leg_trigger;
    char cal_leg_sel;
    char cal_arm_trigger;                                                                   
    char cal_arm_sel;       
    char cal_imu_trigger;                                                                   
    char cal_imu_sel;                                                              
    char ip_buf[20];
} _robot_lvgl;

extern _robot_lvgl robot_lvgl;

#if 0
    /* 链接wifi名称 */
    #define DEFAULT_SSID        "Tinker-2.4G-3"
    #define DEFAULT_PWD         "11111111"
    /* 需要自己设置远程IP地址 */
    #define IP_ADDR   "192.168.1.11" //目标机IP地址
    #define LWIP_DEMO_PORT               8080    /* 目标端口 */
    #define LWIP_DEMO_RX_BUFSIZE         1024    /* 最大接收数据长度 */
#else
    /* 链接wifi名称 */
    #define DEFAULT_SSID        "LBm"
    #define DEFAULT_PWD         "11111111"
    /* 需要自己设置远程IP地址 */
    #define IP_ADDR   "192.168.1.11" //目标机IP地址
    #define LWIP_DEMO_PORT               7070    /* 目标端口 */
    #define LWIP_DEMO_RX_BUFSIZE         1024    /* 最大接收数据长度 */
#endif

#endif

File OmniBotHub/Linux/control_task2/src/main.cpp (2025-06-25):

#include <sys/shm.h>
#include <stdint.h>
#include <unistd.h>
#include <stdio.h>
#include <stdlib.h>
#include <getopt.h>
#include <fcntl.h>
#include <sys/ioctl.h>
#include <linux/types.h>
#include <linux/spi/spidev.h>
#include <string.h>
#include <iostream>
#include <sstream>
#include <stdio.h>
#include <unistd.h>
#include <stdio.h>
#include <sys/time.h>
#include <math.h>
#include <time.h>
#include "comm.h"
#include "spi_node.h"
#include "sys_time.h"
#include "include.h"
#include "gait_math.h"
#include "can.h"
#include "locomotion_header.h"
#include <pthread.h>
#include <qpOASES.hpp>
#include <sys/types.h>
#include <sys/socket.h>
#include <netinet/in.h>
#include <pthread.h>
#include "eso_RL.h"

#define SERV_PORT_MAP   6666
pid_t pid_control,pid_servo,pid_mpc,pid_nav;
// ps -ef | grep control_task   ps a全部查看
// ps -ef | grep hardware_task
// kill －9 324  ps aux | grep "XXX"
// sudo nano /etc/rc.local
#define MUL_THREAD 1
#define USE_MAP    0
using namespace qpOASES;
pthread_mutex_t lock;
pthread_mutex_t lock_mpc;

void setCurrentThreadHighPriority(bool value) {
#if 1
  // Start out with a standard, low-priority setup for the sched params.
  struct sched_param sp;
  bzero((void*)&sp, sizeof(sp));
  int policy = SCHED_OTHER;

  // If desired, set up high-priority sched params structure.
  if (value) {
    // FIFO scheduler, ranked above default SCHED_OTHER queue
    policy = SCHED_FIFO;
    // The priority only compares us to other SCHED_FIFO threads, so we
    // just pick a random priority halfway between min & max.
    const int priority = (sched_get_priority_max(policy) + sched_get_priority_min(policy)) / 2;

    sp.sched_priority = priority;
  }

  // Actually set the sched params for the current thread.
  if (0 == pthread_setschedparam(pthread_self(), policy, &sp)) {
    printf("IO Thread using high-priority scheduler!\n");
  }
#endif
}

void Perror(const char *s)
{
    perror(s);
    exit(EXIT_FAILURE);
}

static void setnonblocking(int sockfd) {
    int flag = fcntl(sockfd, F_GETFL, 0);
    if (flag < 0) {
        Perror("fcntl F_GETFL fail");
        return;
    }
    if (fcntl(sockfd, F_SETFL, flag | O_NONBLOCK) < 0) {
        Perror("fcntl F_SETFL fail");
    }
}

void rc_process(float T){
    float FLT_RC=0;
    static char key_st_reg=0,key_a_reg=0,key_selet_reg,request_mode_reg=0;
    static char aux_smart_reg=0;
    static char rc_interuped=0;
    static float rc_interuped_cnt=0;
    float weight_yaw,err_yaw;

     if(ocu.mode==RC_REMOTE){//auto mode
        if(key_st_reg==0&&ocu.key_st==1&&gait_ww.state_gait==2)
        {
            if(sdk.sdk_mode==0){
                sdk.sdk_mode=1;
                printf("Control:: Enable SDK command!\n");
            }else{
                sdk.sdk_mode=0;
                printf("Control:: Disable SDK command!\n");
            }
        }else if(key_a_reg==0&&sdk.sdk_mode==1&&(ocu.key_a==1||ocu.key_b==1||ocu.key_y==1)){
                sdk.sdk_mode=0;
                printf("Control:: Disable SDK command!\n");
        }
     }

     if(request_mode_reg!=nav_tx.request_gait){//control by ros
        if(nav_tx.request_gait==100){
            sdk.sdk_mode=1;
            printf("ROS API:: Enable SDK command!\n");
        }
        else if(nav_tx.request_gait==101){
            sdk.sdk_mode=0;
            printf("ROS API:: Disable SDK command!\n");
        }else if(nav_tx.request_gait==102){
            sdk.sdk_mode=0;
            ocu.key_ud=-1;
            printf("ROS API:: Force Safe command!\n");
        }
     }
     request_mode_reg=nav_tx.request_gait;

     if(ocu.esp32_connect){
         sdk.sdk_mode=ocu.auto_mode;
         if(ocu.auto_mode==1)//enable auto
            nav_tx.request_gait=100;
         else
            nav_tx.request_gait=99;
     }

     //printf("request_gait=%d ouc=%d sbus=%d uwb=%d en_sdk=%d\n",nav_tx.request_gait,ocu.connect,ocu.sbus_conncect,sdk_tar_way_point_uwb.check,sdk.sdk_mode) ;
     if((ocu.connect||sdk.sdk_mode==1||ocu.esp32_connect)&&sdk.sdk_mode==0){//nav_tx.request_gait==99){

          ocu.rc_spd_w[Yr]=dead(ocu.rc_spd_w[Yr],0.15);
          if(ocu.mode==RC_REMOTE||ocu.esp32_connect){
             switch(vmc_all.gait_mode){
                 default:
                    FLT_RC=0.68;
                    DigitalLPF(ocu.rc_spd_w[Xr]*MAX_SPD_X,&vmc_all.tar_spd.x,FLT_RC,T);
                    DigitalLPF(ocu.rc_spd_w[Yr]*MAX_SPD_Y,&vmc_all.tar_spd.y,FLT_RC/2,T);
                    DigitalLPF(ocu.rate_yaw_w*MAX_SPD_RAD,&vmc_all.tar_spd.z,FLT_RC/2,T);
                    DigitalLPF(ocu.rc_att_w[PITr]*vmc_all.param.MAX_PIT,&vmc_all.tar_att[PITr],FLT_RC,T);
                    DigitalLPF(ocu.rc_att_w[ROLr]*vmc_all.param.MAX_ROL, &vmc_all.tar_att[ROLr],FLT_RC/2,T);
                 break;
             }
          }
          //printf("%f %f %f\n",ocu.rc_spd_w[Xr],ocu.rc_spd_w[Yr],ocu.rate_yaw_w);
         if(ABS(vmc_all.tar_spd.x)>MIN_SPD_ST||ABS(vmc_all.tar_spd.y)>MIN_SPD_ST)
            vmc_all.param.have_cmd_rc[0]=1;
         else
            vmc_all.param.have_cmd_rc[0]=0;
         if(ABS(vmc_all.tar_spd.z)>MIN_SPD_ST_RAD)
            vmc_all.param.have_cmd_rc[1]=1;
         else
            vmc_all.param.have_cmd_rc[1]=0;

     }
     else if(sdk.sdk_mode==1)//nav_tx.request_gait!=99)//SDK commond Use ROS=============================
     {
        printf("ssrc_interuped=%d sdk.sdk_mode=%d sdk.cmd_vyaw=%f %f %f sdk.sdk_mode=%d\n",rc_interuped,sdk.sdk_mode,sdk.cmd_vx,sdk.cmd_vy,sdk.cmd_vyaw,sdk.sdk_mode);
        if(rc_interuped||sdk.cmd_vyaw==-1||sdk.sdk_mode==0){//rc interupte
            MAX_SPD=MAX_FSPD;
            switch(vmc_all.gait_mode){
                default:
                   FLT_RC=1.68;
                   DigitalLPF(ocu.rc_spd_w[Xr]*MAX_SPD,&vmc_all.tar_spd.x,FLT_RC,T);
                   DigitalLPF(ocu.rc_spd_w[Yr]*MAX_SPD,&vmc_all.tar_spd.y,FLT_RC/2,T);
                   DigitalLPF(ocu.rate_yaw_w*MAX_SPD_RAD,&vmc_all.tar_spd.z,FLT_RC,T);
                   DigitalLPF(ocu.rc_att_w[PITr]*vmc_all.param.MAX_PIT,&vmc_all.tar_att[PITr],FLT_RC,T);
                   DigitalLPF(ocu.rc_att_w[ROLr]*vmc_all.param.MAX_ROL, &vmc_all.tar_att[ROLr],FLT_RC/2,T);
                break;
            }

            if((fabs(ocu.rc_spd_w[Xr])>0.1||ocu.rc_spd_w[Yr]>0.1||ocu.rate_yaw_w>0.1)&&!rc_interuped)
                {rc_interuped=1;rc_interuped_cnt=0;printf("Control:: Disable SDK for RC interuped!\n");		}
            if((fabs(ocu.rc_spd_w[Xr])<0.1&&ocu.rc_spd_w[Yr]<0.1&&ocu.rate_yaw_w<0.1)&&rc_interuped==1)
                rc_interuped_cnt+=T;
            else
                rc_interuped_cnt=0;

            if(rc_interuped_cnt>2&&rc_interuped==1)
                {rc_interuped=0;printf("Control:: Re-enable SDK command without RC!\n");}
        }else{//SDK control====================================
            FLT_RC=1.0;
            DigitalLPF(sdk.cmd_vx,&vmc_all.tar_spd.x,FLT_RC/3,T);
            DigitalLPF(sdk.cmd_vy,&vmc_all.tar_spd.y,FLT_RC/2,T);
            DigitalLPF(sdk.cmd_vyaw*57.3,&vmc_all.tar_spd.z,FLT_RC,T);

            vmc_all.tar_spd.x=LIMIT(vmc_all.tar_spd.x,-MAX_SPD,MAX_SPD);
            vmc_all.tar_spd.y=LIMIT(vmc_all.tar_spd.y,-MAX_SPD,MAX_SPD);

            DigitalLPF(sdk.cmd_pit,&vmc_all.tar_att[PITr],FLT_RC,T);
            DigitalLPF(sdk.cmd_rol, &vmc_all.tar_att[ROLr],FLT_RC,T);
        }

         if(ABS(vmc_all.tar_spd.x)>MIN_SPD_ST||ABS(vmc_all.tar_spd.y)>MIN_SPD_ST)
            vmc_all.param.have_cmd_rc[0]=1;
         else
            vmc_all.param.have_cmd_rc[0]=0;
         if(ABS(vmc_all.tar_spd.z)>MIN_SPD_ST_RAD)
            vmc_all.param.have_cmd_rc[1]=1;
         else
            vmc_all.param.have_cmd_rc[1]=0;
     }
     else{
          FLT_RC=0.86;
          DigitalLPF(0,&vmc_all.tar_spd.x,FLT_RC/4,T);
          DigitalLPF(0,&vmc_all.tar_spd.y,FLT_RC/4,T);
          DigitalLPF(0,&vmc_all.tar_spd.z,FLT_RC,T);
          DigitalLPF(0,&vmc_all.tar_att[PITr],FLT_RC/2,T);
          DigitalLPF(0,&vmc_all.tar_att[ROLr],0.068,T);
      }

  //----------------------Beep Reset---------------
      static int beep_changing=0;
      static float beep_timer=0;
      if(robotwb.beep_state!=0&&!beep_changing)
         { beep_changing=1;beep_timer=0;}
      if(beep_changing)
          beep_timer+=T;
      if(beep_timer>2)
          robotwb.beep_state=beep_timer=beep_changing=0;

    key_a_reg=ocu.key_a;
    key_st_reg=ocu.key_st;
    key_selet_reg=ocu.key_back;
    aux_smart_reg=spi_rx.ocu.sbus_aux[3];
}

void* Thread_T1(void*)//控制线程
{
    float timer[5]={0};
    float sys_dt = 0,dT=0,T;
    int i=0;
    CAN_motor_init();
    for (i = 0; i < 4; i++) {
        cal_jacobi_new(&vmc[i], 0.002);	//计算雅克比
        cal_invjacobi(&vmc[i]);		//计算雅克比逆
    }

    setCurrentThreadHighPriority(11);

    while(1)
    {
        float leg_dt[2]={0};
        T = Get_Cycle_T(31);
        leg_dt[1]=T;
        subscribe_imu_to_webot(&robotwb, T);//赋值给robot结构体

        readAllMotorPos(&robotwb, leg_dt[1]);//读取角度

        locomotion_sfm(leg_dt[1]);//摆动控制

        if(vmc_all.gait_mode==G_RL )
            force_control_and_dis_rl(leg_dt[1]);//位力混控 TORT版本
        else//default
            force_control_and_dis_stand(leg_dt[1]);//位力混控 站立版本

        if(T>0.005)
            printf("OT-S::sys_dt=%f\n",T);

        usleep(2000);
    }
}

void* Thread_T5(void*)//控制线程
{

    float timer[5]={0};
    float sys_dt = 0,dT=0;
    int i=0;

    while(1)
    {
        dT = Get_Cycle_T(32);
        rc_process(dT);

        usleep(5*1000);
        if(dT>0.0055)
            printf("OT-C::sys_dt=%f\n",dT);
    }
}

//--------------------------------------------------------------------------------------------
struct recv_msg
{
      char flag_map;
      int16_t map2d_local[80*80];
      float odom_pos[3];
      float odom_spd[3];
      float odom_att[3];
      float odom_rate[3];
} _recv_msg;

struct send_msg
{
      float euler[3];
      float omega[3];
      float velxyz[3];
} _send_msg;


void* Thread_UDP_MAP(void*)//SDK UDP通讯线程-------------MAP Divide
{
    static int mode_reg=0;
    static int cnt = 0;
    int map_lsm=0;
    float odom_z_off=0;
    float sys_dt = 0;
    int flag = 0;
    float timer[5]={0};
    int i=0;

    int sock_fd = socket(AF_INET, SOCK_DGRAM, 0);
    if(sock_fd < 0)
    {
        perror("socket");
        exit(1);
    }
   setnonblocking(sock_fd);//非阻塞
   struct sockaddr_in addr_serv;
   int len;

   memset(&addr_serv, 0, sizeof(struct sockaddr_in));  //每个字节都用0填充
   addr_serv.sin_family = AF_INET;//使用IPV4地址
   addr_serv.sin_port = htons(SERV_PORT_MAP);//端口
   addr_serv.sin_addr.s_addr = htonl(INADDR_ANY);  //自动获取IP地址
   len = sizeof(addr_serv);

   if(bind(sock_fd, (struct sockaddr *)&addr_serv, sizeof(addr_serv)) < 0)
   {
     perror("bind error:");
     exit(1);
   }

    int recv_num=0,send_num=0;
    char send_buf[500]={0},recv_buf[1024*30]={0};
    struct sockaddr_in addr_client;
    while (1)
    {
        sys_dt = Get_Cycle_T(12);
        timer[0]+=sys_dt;

        //读取客户端
        recv_num = recvfrom(sock_fd, recv_buf, sizeof(recv_buf), MSG_DONTWAIT, (struct sockaddr *)&addr_client, (socklen_t *)&len);
        //printf("recv_num=%d\n",recv_num);
        if(recv_num <= 0)
        {
            //perror("OCU recvfrom error:");
            //exit(1);
        }
        else{
        //解码
            memcpy(&_recv_msg,recv_buf,sizeof(_recv_msg));

            mode_reg=vmc_all.gait_mode;
            //send_num = sendto(sock_fd, send_buf, usb_send_cnt, MSG_DONTWAIT, (struct sockaddr *)&addr_client, len);
            //printf("usb_send_cnt=%d\n",usb_send_cnt);
            if(send_num < 0)
            {
                perror("MAP sendto error:");
                exit(1);
            }

        }
        usleep(50*1000);
    }
    close(sock_fd);
    return 0;
}

//RL
struct _msg_request_tinymal
{
    float trigger;
    float command[4];
    float eu_ang[3];
    float omega[3];
    float acc[3];
    float q[12];
    float dq[12];
    float tau[12];
    float q_init[12];
} _msg_request_tinymal;

struct _msg_response_tinymal
{
    float q_exp[12];
    float dq_exp[12];
    float tau_exp[12];
} _msg_response_tinymal;

void* Thread_UDP_RL_Tinymal(void*)//RL Service
{
    static int cnt = 0;
    float sys_dt = 0;
    float loss_cnt_sdk=0;
    int flag = 0;
    float timer[5]={0};
    int i=0;

    int sock_fd = socket(AF_INET, SOCK_DGRAM, 0);
    if(sock_fd < 0)
    {
        perror("socket");
        exit(1);
    }
   setnonblocking(sock_fd);//非阻塞
   struct sockaddr_in addr_serv;
   int len;
   memset(&addr_serv, 0, sizeof(struct sockaddr_in));  //每个字节都用0填充
   addr_serv.sin_family = AF_INET;//使用IPV4地址
   addr_serv.sin_port = htons(10000);//端口<-----------------Python
   addr_serv.sin_addr.s_addr = htonl(INADDR_ANY);  //自动获取IP地址
   len = sizeof(addr_serv);

   if(bind(sock_fd, (struct sockaddr *)&addr_serv, sizeof(addr_serv)) < 0)
   {
     perror("bind error:");
     exit(1);
   }
    int id_list[12]={0,1,2,3,4,5, 7,8,9,10,11,12};
    int recv_num=0,send_num=0;
    int recording_flag=0;
    char send_buf[500]={0},recv_buf[500]={0};
    struct sockaddr_in addr_client;
    int cnt_p=0;
    printf("Thread UDP Master RL-Tinymal\n");
#if 0
    vmc_all.default_action[0]=-0.16;
    vmc_all.default_action[1]=0.68;
    vmc_all.default_action[2]=1.3;

    vmc_all.default_action[3]=0.16;
    vmc_all.default_action[4]=0.68;
    vmc_all.default_action[5]=1.3;

    vmc_all.default_action[6]=-0.16;
    vmc_all.default_action[7]=0.68;
    vmc_all.default_action[8]=1.3;

    vmc_all.default_action[9]=0.16;
    vmc_all.default_action[10]=0.68;
    vmc_all.default_action[11]=1.3;
    vmc_all.sita3_off=175;
#endif
    while (1)
    {
        recv_num = recvfrom(sock_fd, recv_buf, sizeof(recv_buf), 0, (struct sockaddr *)&addr_client, (socklen_t *)&len);
        vmc_all.loss_rl++;
        if(vmc_all.loss_rl>100)
            vmc_all.rl_connect=0;
        if(recv_num >0)
        {   //--------------actions---------------
            vmc_all.rl_connect=1;
            vmc_all.loss_rl=0;
            memcpy(&_msg_response_tinymal,recv_buf,sizeof(_msg_response_tinymal));
            if(vmc_all.gait_mode==G_RL){
                for(int i=0;i<12;i++){
                    float temp=LIMIT(_msg_response_tinymal.q_exp[i],-5,5)*vmc_all.action_scale+vmc_all.default_action[id_list[i]];//action scale->0.25 good 50Hz
                    leg_motor_all.q_set[id_list[i]]=LIMIT(temp*57.3,leg_motor_all.q_min[id_list[i]],leg_motor_all.q_max[id_list[i]]);
                    leg_motor_all.q_set[id_list[i]]=temp*57.3;
                }
                //printf("action:%.3f %.3f %.3f\n",_msg_response_tinker.q_exp[0],_msg_response_tinker.q_exp[1],_msg_response_tinker.q_exp[2]);
            }
            //---------------obs------------------
            sys_dt = Get_Cycle_T(40);
            timer[0]+=sys_dt;
            if(timer[0]>vmc_all.net_run_dt){//50Hz to elav the net
                timer[0]=0;
                _msg_request_tinymal.trigger=1;
            }else
                _msg_request_tinymal.trigger=0;
            _msg_request_tinymal.command[0]=   LIMIT(vmc_all.tar_spd.x*2,-1,1);
            _msg_request_tinymal.command[1]=   LIMIT(-vmc_all.tar_spd.y*4,-1,1);

            if (fabs(vmc_all.tar_spd.z) > 1)
            {
                _msg_request_tinymal.command[2] = vmc_all.tar_spd.z/57.3;
                robotwb.exp_att.yaw = robotwb.now_att.yaw;
            }
            else {
                _msg_request_tinymal.command[2] = -dead(limitw(To_180_degrees(robotwb.exp_att.yaw - robotwb.now_att.yaw), -25, 25), 0.25)*1.4/57.3;
            }
            _msg_request_tinymal.command[2]=   LIMIT(_msg_request_tinymal.command[2],-1,1);

            _msg_request_tinymal.eu_ang[0]=vmc_all.att[ROLr]/57.3;
            _msg_request_tinymal.eu_ang[1]=-vmc_all.att[PITr]/57.3;
            _msg_request_tinymal.eu_ang[2]=-vmc_all.att[YAWr]/57.3;
            _msg_request_tinymal.omega[0]=vmc_all.att_rate[ROLr]/57.3;
            _msg_request_tinymal.omega[1]=-vmc_all.att_rate[PITr]/57.3;
            _msg_request_tinymal.omega[2]=vmc_all.att_rate[YAWr]/57.3;

            for(int i=0;i<12;i++){
                _msg_request_tinymal.q[i]=leg_motor_all.q_now[id_list[i]]/57.3;
                _msg_request_tinymal.dq[i]=leg_motor_all.qd_now[id_list[i]]/57.3;
                _msg_request_tinymal.q_init[i]=vmc_all.default_action[id_list[i]];
            }

            //--------------------------For switch
            if(vmc_all.gait_mode!=G_RL){
                _msg_request_tinymal.eu_ang[0]=0;
                _msg_request_tinymal.eu_ang[1]=0;
                _msg_request_tinymal.eu_ang[2]=0;
                _msg_request_tinymal.omega[0]=0;
                _msg_request_tinymal.omega[1]=0;
                _msg_request_tinymal.omega[2]=0;

                for(int i=0;i<12;i++){
                    _msg_request_tinymal.q[i]=vmc_all.default_action[id_list[i]];
                    _msg_request_tinymal.dq[i]=0;
                    _msg_request_tinymal.q_init[i]=vmc_all.default_action[id_list[i]];
                }
            }
            memcpy(send_buf,&_msg_request_tinymal,sizeof(_msg_request_tinymal));
            send_num = sendto(sock_fd, send_buf, sizeof(_msg_request_tinymal), MSG_DONTWAIT, (struct sockaddr *)&addr_client, len);
            if(send_num < 0)
            {
                perror("OCU sendto error:");
                exit(1);
            }
        }
        usleep(2*1000);//
    }
    close(sock_fd);
    return 0;
}
//RL UDP
struct _msg_request_tinker
{
    float trigger;
    float command[4];
    float eu_ang[3];
    float omega[3];
    float acc[3];
    float q[10];
    float dq[10];
    float tau[10];
    float q_init[10];
} _msg_request_tinker;

struct _msg_response_tinker
{
    float q_exp[10];
    float dq_exp[10];
    float tau_exp[10];
} _msg_response_tinker;

void* Thread_UDP_RL_Tinker(void*)//RL Service
{
    static int cnt = 0;
    float sys_dt = 0;
    float loss_cnt_sdk=0;
    int flag = 0;
    float timer[5]={0};
    int i=0;

    int sock_fd = socket(AF_INET, SOCK_DGRAM, 0);
    if(sock_fd < 0)
    {
        perror("socket");
        exit(1);
    }
   setnonblocking(sock_fd);//非阻塞
   struct sockaddr_in addr_serv;
   int len;
   memset(&addr_serv, 0, sizeof(struct sockaddr_in));  //每个字节都用0填充
   addr_serv.sin_family = AF_INET;//使用IPV4地址
   addr_serv.sin_port = htons(10000);//端口<-----------------Python
   addr_serv.sin_addr.s_addr = htonl(INADDR_ANY);  //自动获取IP地址
   len = sizeof(addr_serv);

   if(bind(sock_fd, (struct sockaddr *)&addr_serv, sizeof(addr_serv)) < 0)
   {
     perror("bind error:");
     exit(1);
   }

    int recv_num=0,send_num=0;
    int recording_flag=0;
    char send_buf[500]={0},recv_buf[500]={0};
    struct sockaddr_in addr_client;
    int cnt_p=0;
    int id_list[10]={0,1,2,3,4, 7,8,9,10,11};
    printf("Thread UDP Master RL-Tinker14\n");
#if 0
    vmc_all.default_action[0]=0.0;
    vmc_all.default_action[1]=-0.07;
    vmc_all.default_action[2]=0.56;
    vmc_all.default_action[3]=-1.12;
    vmc_all.default_action[4]=0.57;

    vmc_all.default_action[7]=0.0;
    vmc_all.default_action[8]=0.07;
    vmc_all.default_action[9]=0.56;
    vmc_all.default_action[10]=-1.12;
    vmc_all.default_action[11]=0.57;
#endif
    while (1)//sim 0->left 1->right
    {
        recv_num = recvfrom(sock_fd, recv_buf, sizeof(recv_buf), 0, (struct sockaddr *)&addr_client, (socklen_t *)&len);
        vmc_all.loss_rl++;
        if(vmc_all.loss_rl>100)
            vmc_all.rl_connect=0;
#if HEAD_USE_DC//tinker head control
        if(gait_ww.state_gait>=2){
            DigitalLPF(ocu.rc_att_w[PITr]*50,&leg_motor_all.q_set[5],0.9,0.005);//pitch
            leg_motor_all.q_set[5]=LIMIT(leg_motor_all.q_set[5],-35,60);
            DigitalLPF(-ocu.rc_att_w[ROLr]*70,&leg_motor_all.q_set[6],0.8,0.005);//yaw
        }
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
int main(int argc, char *argv[])
{
    pthread_t tid_servo, tid_control, tid_nav, tid_mpc,tid_map,tid_rl,tid_ocu,tid_t[10];
#if 0
    cpu_set_t mask;
    CPU_ZERO(&mask);
    CPU_SET(3, &mask);
    if (sched_setaffinity(0, sizeof(mask), &mask) < 0) {
    perror("sched_setaffinity");
    }
#endif
    pthread_mutex_init(&lock, NULL);
    pthread_mutex_init(&lock_mpc, NULL);

#if MUL_THREAD&&!THREAD_2
    pthread_create(&tid_servo, NULL, Thread_Mem_Servo, NULL);
#endif

#if !THREAD_2
    pthread_create(&tid_nav, NULL, Thread_Mem_Navigation, NULL);
#endif
#if !THREAD_1
    pthread_create(&tid_t[0], NULL, Thread_T5, NULL);
    pthread_create(&tid_t[1], NULL, Thread_T1, NULL);
#endif

#if USE_RL&&!RL_USE_TVM
    pthread_create(&tid_rl, NULL, Thread_UDP_RL_Tinker, NULL);
    //pthread_create(&tid_rl, NULL, Thread_UDP_RL_Tinymal, NULL);
#endif
    pthread_create(&tid_ocu, NULL, Thread_UDP_OCU, NULL);
#if MUL_THREAD
    pthread_join(tid_servo, NULL);
#endif

#if !THREAD_1
    pthread_join(tid_t[0], NULL);
    pthread_join(tid_t[1], NULL);
#endif
#if !THREAD_2
    pthread_join(tid_nav, NULL);
#endif
#if USE_RL
    pthread_join(tid_rl, NULL);
#endif
    pthread_join(tid_ocu, NULL);
    return 1;
}

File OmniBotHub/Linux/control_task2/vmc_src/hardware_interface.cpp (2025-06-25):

#include "include.h"
#include "locomotion_header.h"
#include "can.h"
#include "gait_math.h"
#if RUN_WEBOTS&&!RUN_PI
#include "wbInterface.h"
#endif
#if RUN_PI
#include "spi_node.h"
#endif
_TD4 bldc_td4[4][3];
float FLT_ATT_RATE=0;//WS
#define USE_TD4_RATE 1

void subscribe_imu_to_webot(robotTypeDef* rob,float dt)
{
    if (vmc_all.side_flip == 0) {
            robotwb.IMU_now.pitch= robotwb.IMU_now_o.pitch;
            robotwb.IMU_now.roll= robotwb.IMU_now_o.roll;
            robotwb.IMU_now.yaw= robotwb.IMU_now_o.yaw;
            robotwb.IMU_dot.pitch= robotwb.IMU_dot_o.pitch;
            robotwb.IMU_dot.roll= robotwb.IMU_dot_o.roll;
            robotwb.IMU_dot.yaw= robotwb.IMU_dot_o.yaw;
    }
    else {//翻转  机头方向不变
        if (robotwb.IMU_now_o.pitch > 0)
             robotwb.IMU_now.pitch =  (180 - robotwb.IMU_now_o.pitch);
        else
            robotwb.IMU_now.pitch  =  -(180 + robotwb.IMU_now_o.pitch);

        robotwb.IMU_now.roll= -robotwb.IMU_now_o.roll;

        if(robotwb.IMU_now_o.yaw>0)
            robotwb.IMU_now.yaw= -(180-robotwb.IMU_now_o.yaw);
        else
            robotwb.IMU_now.yaw= (180+robotwb.IMU_now_o.yaw);

        robotwb.IMU_dot.pitch= -robotwb.IMU_dot_o.pitch;
        robotwb.IMU_dot.roll= robotwb.IMU_dot_o.roll;
        robotwb.IMU_dot.yaw= -robotwb.IMU_dot_o.yaw;
    }

    vmc_all.att[PITr]= robotwb.IMU_now.pitch;
    vmc_all.att[ROLr]= robotwb.IMU_now.roll;
    vmc_all.att[YAWr]= robotwb.IMU_now.yaw;
#if FLIP_TEST&&0
    printf("pit=%f rol=%f yaw=%f\n",vmc_all.att[PITr],vmc_all.att[ROLr],vmc_all.att[YAWr]);
    printf("dpit=%f drol=%f dyaw=%f\n",vmc_all.att_rate[PITr],vmc_all.att_rate[ROLr],vmc_all.att_rate[YAWr]);
#endif
    vmc_all.att_rate[PITr]=robotwb.IMU_dot.pitch;
    vmc_all.att_rate[ROLr]=robotwb.IMU_dot.roll;
    vmc_all.att_rate[YAWr]=robotwb.IMU_dot.yaw;

    static float att_rt_use[3] = {0};
    DigitalLPF(vmc_all.att[PITr], &att_rt_use[PITr], 0, dt);
    DigitalLPF(vmc_all.att[ROLr], &att_rt_use[ROLr], 0, dt);
    DigitalLPF(vmc_all.att[YAWr], &att_rt_use[YAWr], 0, dt);

    vmc_all.Rnn_b[0][0] = cosd(-att_rt_use[PITr])*cosd(-att_rt_use[YAWr]);
    vmc_all.Rnn_b[1][0] = -cosd(-att_rt_use[ROLr])*sind(-att_rt_use[YAWr]) + sind(-att_rt_use[PITr])*sind(-att_rt_use[ROLr])*cosd(-att_rt_use[YAWr]);
    vmc_all.Rnn_b[2][0] = sind(-att_rt_use[ROLr])*sind(-att_rt_use[YAWr]) + cosd(-att_rt_use[ROLr])*sind(-att_rt_use[PITr])*cosd(-att_rt_use[YAWr]);

    vmc_all.Rnn_b[0][1] = cosd(-att_rt_use[PITr])*sind(-att_rt_use[YAWr]);
    vmc_all.Rnn_b[1][1] = cosd(-att_rt_use[ROLr])*cosd(-att_rt_use[YAWr]) + sind(-att_rt_use[ROLr])*sind(-att_rt_use[PITr])*sind(-att_rt_use[YAWr]);
    vmc_all.Rnn_b[2][1] = -sind(-att_rt_use[ROLr])*cosd(-att_rt_use[YAWr]) + cosd(-att_rt_use[ROLr])*sind(-att_rt_use[PITr])*sind(-att_rt_use[YAWr]);

    vmc_all.Rnn_b[0][2] = -sind(-att_rt_use[PITr]);
    vmc_all.Rnn_b[1][2] = sind(-att_rt_use[ROLr])*cosd(-att_rt_use[PITr]);
    vmc_all.Rnn_b[2][2] = cosd(-att_rt_use[ROLr])*cosd(-att_rt_use[PITr]);

    mat_trans(vmc_all.Rnn_b, vmc_all.Rb_nn);

    att_rt_use[YAWr] = 0;
    vmc_all.Rn_b[0][0] = cosd(-att_rt_use[PITr])*cosd(-att_rt_use[YAWr]);
    vmc_all.Rn_b[1][0] = -cosd(-att_rt_use[ROLr])*sind(-att_rt_use[YAWr]) + sind(-att_rt_use[PITr])*sind(-att_rt_use[ROLr])*cosd(-att_rt_use[YAWr]);
    vmc_all.Rn_b[2][0] = sind(-att_rt_use[ROLr])*sind(-att_rt_use[YAWr]) + cosd(-att_rt_use[ROLr])*sind(-att_rt_use[PITr])*cosd(-att_rt_use[YAWr]);

    vmc_all.Rn_b[0][1] = cosd(-att_rt_use[PITr])*sind(-att_rt_use[YAWr]);
    vmc_all.Rn_b[1][1] = cosd(-att_rt_use[ROLr])*cosd(-att_rt_use[YAWr]) + sind(-att_rt_use[ROLr])*sind(-att_rt_use[PITr])*sind(-att_rt_use[YAWr]);
    vmc_all.Rn_b[2][1] = -sind(-att_rt_use[ROLr])*cosd(-att_rt_use[YAWr]) + cosd(-att_rt_use[ROLr])*sind(-att_rt_use[PITr])*sind(-att_rt_use[YAWr]);

    vmc_all.Rn_b[0][2] = -sind(-att_rt_use[PITr]);
    vmc_all.Rn_b[1][2] = sind(-att_rt_use[ROLr])*cosd(-att_rt_use[PITr]);
    vmc_all.Rn_b[2][2] = cosd(-att_rt_use[ROLr])*cosd(-att_rt_use[PITr]);

    mat_trans(vmc_all.Rn_b, vmc_all.Rb_n);

    if(vmc_all.param.leg_dof==2)
        att_rt_use[ROLr]=0;
    att_rt_use[YAWr]=0;
    vmc_all.Rn_b_noroll[0][0] =  cosd(-att_rt_use[PITr])*cosd(-att_rt_use[YAWr]);
    vmc_all.Rn_b_noroll[1][0] = -cosd(-att_rt_use[ROLr])*sind(-att_rt_use[YAWr])+sind(-att_rt_use[PITr])*sind(-att_rt_use[ROLr])*cosd(-att_rt_use[YAWr])  ;
    vmc_all.Rn_b_noroll[2][0] =  sind(-att_rt_use[ROLr])*sind(-att_rt_use[YAWr])+cosd(-att_rt_use[ROLr])*sind(-att_rt_use[PITr])*cosd(-att_rt_use[YAWr])  ;

    vmc_all.Rn_b_noroll[0][1] =  cosd(-att_rt_use[PITr])*sind(-att_rt_use[YAWr]);
    vmc_all.Rn_b_noroll[1][1] =  cosd(-att_rt_use[ROLr])*cosd(-att_rt_use[YAWr])+sind(-att_rt_use[ROLr])*sind(-att_rt_use[PITr])*sind(-att_rt_use[YAWr])  ;
    vmc_all.Rn_b_noroll[2][1] = -sind(-att_rt_use[ROLr])*cosd(-att_rt_use[YAWr])+cosd(-att_rt_use[ROLr])*sind(-att_rt_use[PITr])*sind(-att_rt_use[YAWr])  ;
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

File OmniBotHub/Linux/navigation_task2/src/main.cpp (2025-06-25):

#include <stdint.h>
#include <unistd.h>
#include <stdio.h>
#include <stdlib.h>
#include <getopt.h>
#include <fcntl.h>
#include <sys/ioctl.h>
#include <linux/types.h>
#include <linux/spi/spidev.h>
#include <string.h>
#include <iostream>
#include <sstream>
#include <stdio.h>
#include <unistd.h>
#include <stdio.h>
#include <sys/time.h>
#include <string.h>
#include <unistd.h>
#include <math.h>
#include <time.h>
#include <sys/types.h>
#include <sys/socket.h>
#include <netinet/in.h>
#include <pthread.h>

#include "sys_time.h"
#include "mem_node.h"
#include "base_struct.h"
#include "udp_ocu.h"
#include "comm.h"
#include "can.h"
#include <yaml-cpp/yaml.h>
#include <yaml-cpp/node/parse.h>

YAML::Node config_hardware=YAML::LoadFile("/home/odroid/Tinker/Param/param_hardware.yaml");
//  ps -ef | grep navigation_task
// kill －9 324
#define SERV_PORT       8889
#define SERV_PORT_ARM   9000
#define SERV_PORT_SDK   8888
#define SERV_PORT_MAP   6666

#define MEM_CONTROL 4999
#define MEM_SIZE 2048

#define EN_MAP 0
#define DEMO_KEY 0
_NAV_RX nav_rx;
_NAV_TX nav_tx;

int mem_connect_c=0;
float mem_loss_cnt_c=0;

struct shareMemory
{
    int  flag=0;  //作为一个标志，非0：表示可读，0表示可写
    unsigned char szMsg[MEM_SIZE];
};
struct shareMemory shareMemory_control;
unsigned char mem_read_buf_c[MEM_SIZE];
unsigned char mem_write_buf_c[MEM_SIZE];
int mem_read_cnt_c=0;
int mem_write_cnt_c=0;

pthread_mutex_t lock;

_OCU ocu;
VMC vmc[4];
VMC_ALL vmc_all;
_LEG_MOTOR leg_motor[4];
_SDK moco_sdk;

void Perror(const char *s)
{
    perror(s);
    exit(EXIT_FAILURE);
}

static void setnonblocking(int sockfd) {
    int flag = fcntl(sockfd, F_GETFL, 0);
    if (flag < 0) {
        Perror("fcntl F_GETFL fail");
        return;
    }
    if (fcntl(sockfd, F_SETFL, flag | O_NONBLOCK) < 0) {
        Perror("fcntl F_SETFL fail");
    }
}

struct gait_msg
{
   char gait_mode;
   float att_cmd[3];
   float rate_cmd[3];
   float speed_cmd[3];
   float pos_cmd[3];
} _gait_msg;

static void setDataFloat_mem_c(float f, int *anal_cnt)
{
    int i = *(int *)&f;
    mem_write_buf_c[*anal_cnt+0] = ((i << 24) >> 24);
    mem_write_buf_c[*anal_cnt+1] = ((i << 16) >> 24);
    mem_write_buf_c[*anal_cnt+2] = ((i << 8) >> 24);
    mem_write_buf_c[*anal_cnt+3] = (i >> 24);

    *anal_cnt += 4;
}

static float floatFromData_spi(unsigned char *data, int *anal_cnt)
{
    int i = 0x00;
    i |= (*(data + *anal_cnt + 3) << 24);
    i |= (*(data + *anal_cnt + 2) << 16);
    i |= (*(data + *anal_cnt + 1) << 8);
    i |= (*(data + *anal_cnt + 0));

    *anal_cnt += 4;
    return *(float *)&i;
}

static char charFromData_spi(unsigned char *data, int *anal_cnt)
{
    int temp = *anal_cnt;
    *anal_cnt += 1;
    return *(data + temp);
}
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
